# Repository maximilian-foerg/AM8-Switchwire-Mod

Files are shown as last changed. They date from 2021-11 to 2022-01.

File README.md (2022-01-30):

# AM8 Switchwire Mod

## Table of Contents
1. [Introduction](#introduction)
2. [Renders](#renders)
3. [Some Facts](#some-facts)
4. [Why Core XZ?](#why-core-xz)
5. [Printing Tips](#printing-tips)
6. [Firmware Tips](#firmware-tips)
7. [FAQ](#faq)
8. [BOM (Bill of Materials)](#bom)

## Introduction
This is a Core XZ upgrade for the popular [AM8 frame](https://www.thingiverse.com/thing:2263216) inspired by the Voron Switchwire, which also makes the AM8 compatible with VORON Afterburner.

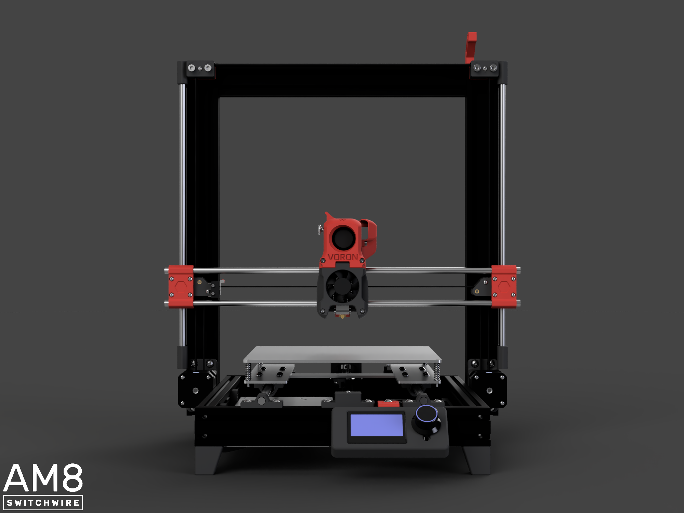
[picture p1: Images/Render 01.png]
Render 01

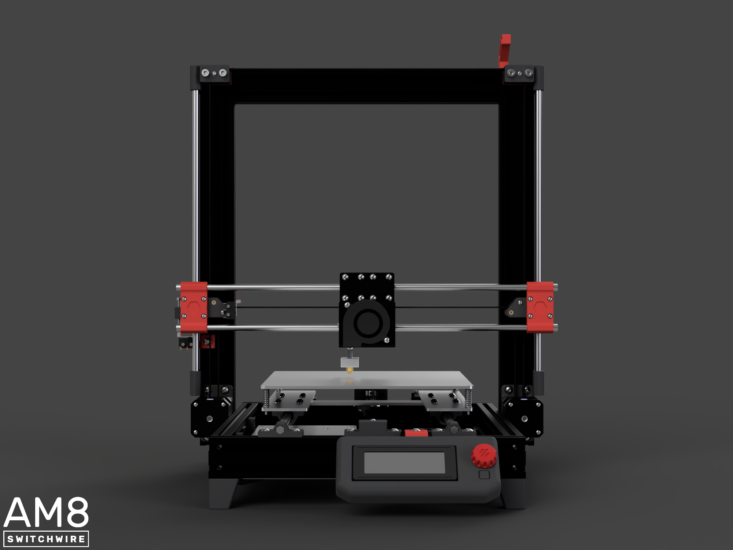
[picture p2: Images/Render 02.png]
Render 02


In case you don't know about the Voron Project, check it out at https://www.vorondesign.com/. They design outstanding open-source 3D printers, and if you're looking for a *real* upgrade, I'd suggest you build a Voron instead. It probably won't get any better.
But if you enjoy tinkering on your cheap 3D printer just like me, this mod could be something for you.

## Renders
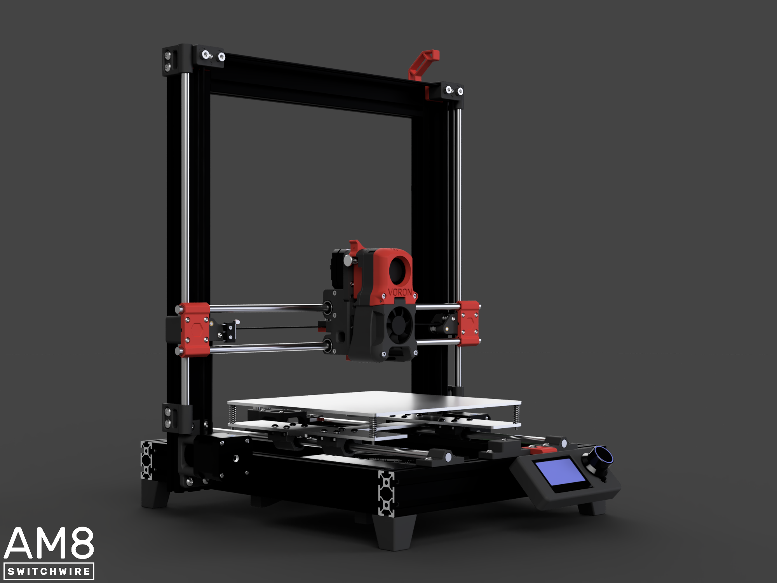
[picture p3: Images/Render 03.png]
Render 03

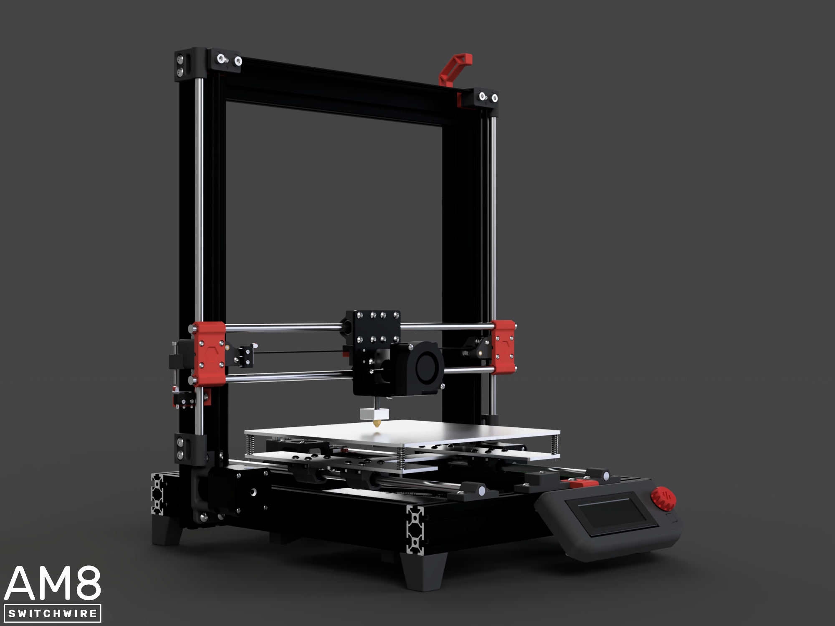
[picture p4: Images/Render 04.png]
Render 04

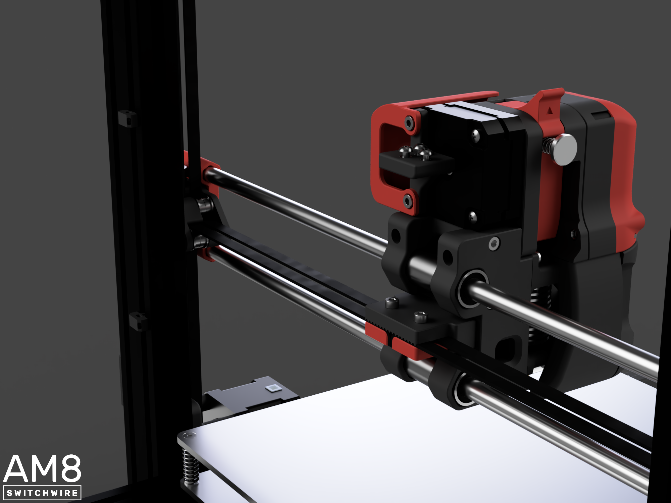
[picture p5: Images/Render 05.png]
Render 05

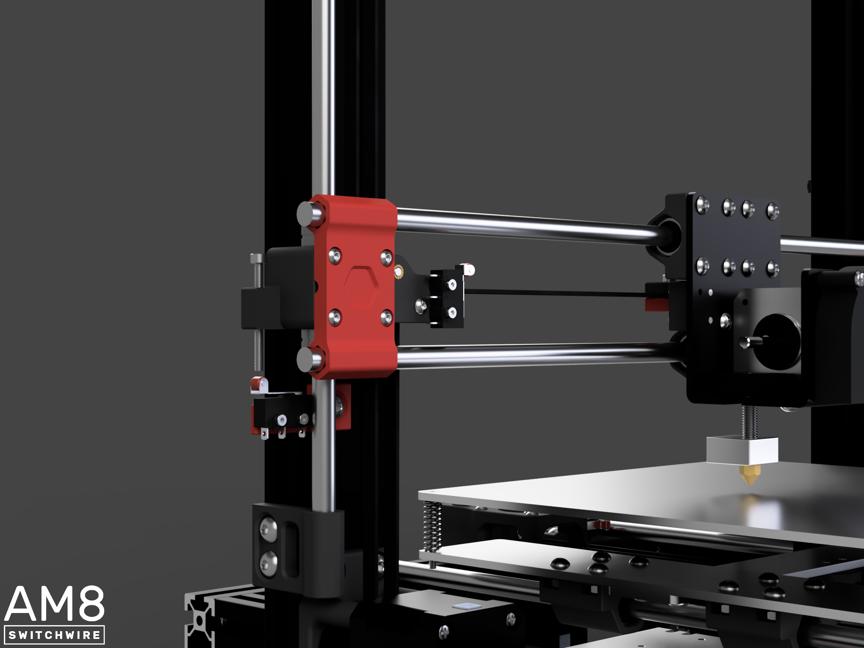
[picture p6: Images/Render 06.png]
Render 06

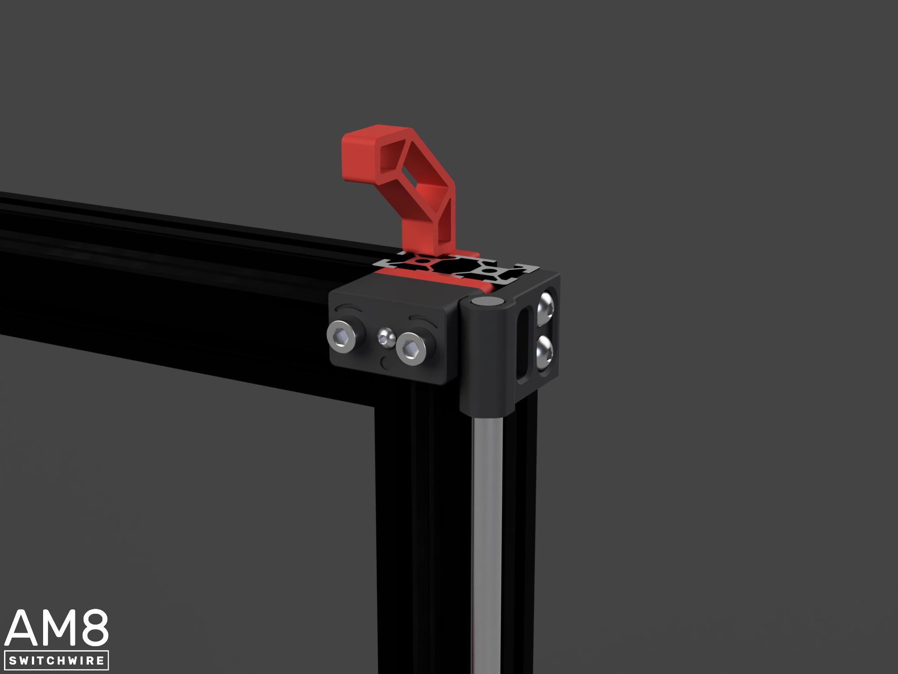
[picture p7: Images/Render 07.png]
Render 07


## Some Facts
* Build volume is 220x220x220mm with Anet A8 print head and up to 220x220x270mm with VORON Afterburner.
* The dimensions of the aluminum extrusions are the same as for the AM8.
* This upgrade uses as many of the original Anet A8 and AM8 parts as possible. Still, you will have to buy some stuff. Have a look at the [BOM](#bom).
* Although I redesigned every part, the Y axis did not change compared to the AM8. So if you already have an AM8, you can continue to use your Y axis.

**_CAUTION!_**
* Altough it would work, **you better not use the original Anet A8 board for this mod**. The Anet A8 board is designed to have two motors connected to the stepper motor driver for the Z axis. Many older versions of the board do not allow you to regulate the voltage for these motors. Since this mod only requires one stepper motor for the Z axis, it would get twice as much current as it should. This could destroy the motor. But it is a good idea to change to a more modern board anyway - especially TMC stepper motor drivers will raise the printer to a new level. My recommendation is the Bigtreetech SKR mini E3 V2. At first glance it may seem expensive, but it has TMC 2209 drivers integrated and is therefore relatively cheap. The TMC drivers allow the voltage for each stepper motor to be controlled individually by software.
* You will have to flash a new firmware (and for the time being, configure it yourself). One possibility is to use [Marlin](https://marlinfw.org/), which can be configured for Core XZ motion systems. My recommendation is [Klipper](https://www.klipper3d.org/) together with a Raspberry Pi running [Mainsail](https://docs.mainsail.xyz/). Klipper runs all calculations on the much more computationally powerful Raspberry Pi, so you can use it to compensate for the weak hardware of the original Anet A8 or other 3D printer controller boards.

## Why Core XZ?
3D printers make fast movements, so it is a great advantage if moving parts have the lowest possible mass. This is why the Core XY architecture was developed, where two stepper motors can move the print head in two directions through a sophisticated belt drive without having to move themselves. Well-known DIY Core XY printers are, for example, the [Voron 0](https://www.vorondesign.com/voron0.1), [Voron Trident](https://www.vorondesign.com/voron_trident) and [Voron 2](https://www.vorondesign.com/voron2.4), or the very popular [Hypercube](https://www.thingiverse.com/thing:1752766) and [Hypercube Evolution](https://www.thingiverse.com/thing:2254103).
However, a Core XY motion system requires a cube-shaped frame, which we do not have with the AM8. Converting the frame would contradict the sense of an "upgrade" and would rather be a completely new printer. Therefore, the [Voron Switchwire](https://www.vorondesign.com/voron_switchwire) gave me the idea to implement the Core XY architecture rotated by 90 degrees as Core XZ architecture on the AM8. This has the following advantages:
* The weight of the X axis is now balanced, because there is no longer a motor on one side.
* The X axis becomes lighter since all stepper motors are fixed to the frame.
* You get rid of the threaded spindles.
* You can make movements in the Z direction just as fast as in the X and Y directions.
* You need one less stepper motor.

## To check before modding your printer
### Extrusions
This mod is using the same aluminium extrusions as the AM8 mod. Extrusions used for designing the parts are Misumi HFSB5-2040, but any 2020 B-type nut 6 extrusions will work.
Make sure your extrusions have these lenghts:
* 3 * 310mm
* 2 * 340mm
* 2 * 440mm

A few mm more or less will work too, as long as the deviations are consistent (f.e. 3 * 313mm is fine, but 2 * 310mm and 1 * 313mm is not).

### Linear Rods
This mod assumes that the original linear rods of the Anet A8 are used. Their lengths are:
* 2 * 436mm
* 4 * 380mm

The required length of the X axis rods is the length of your shortest extrusion + 115mm. So for the spec 310mm extrusions, rods of 425mm in length are required. Longer rods will stick out on the sides, but that's ok.

## Printing Tips
* A number at the end of each file name indicates how often the part must be printed (no number = print it once).
* The `[A]` tag at the beginning of a file name means that this is an accent part. You can print it in an accent color if you like.
* All parts are already oriented for the best printing position. Do not change the orientation. They are specially designed and oriented to be printed without any supports.
* The parts HAVE to be printed in ABS, PETG or another material that can withstand mechanical stress. PLA is NOT an option. Avoid PETG if you have an enclosure for your printer or want to build one, because it bends at high ambient temperatures ("heat creep"). ABS is the best way to go here.
* The parts are designed to be printed with a 0.4mm nozzle at 0.2mm layer height. I recommend the following slicer settings:
  * 4 walls, 5 bottom layers, 5 top layers
  * 40% cubic or gyroid infill
  * No supports
  * No raft
  * Brim or skirt as needed
* Before printing, calibrate your extruder steps and the temperature and flow rate for your specific filament. Get rid of any strining, warping and elephant food on your prints. There are tons of tutorials on the web on how to do each of that.

## Firmware Tips
This sections contains some tips for firmware configuration. Note that the firmware directory contains some configurations.

### General
* Min. Y position: 0
* Max. Y position: 220
* Min. Z position: 0
* Z hop before homing: 5
* DO NOT disable stepper motors (g-code command `M84`) after prints. Print head would fall down on print or bed.
### Anet A8 print head
* Min. X position: -24
* Max. X position: 225
* Max. Z position: 220
* Choose a z hop > 30 if using a level probe instead of the Z endstop switch. This is necessary because if the printhead falls next to the bed after power off, the nozzle protrudes about 30mm below the bed.
### VORON Afterburner print head
* Min. X position: -13
* Max. X position: 240
* Max. Z position: 250

## FAQ
### Why are there three versions of the XZ Axis X Rod Mount (40, 45 and 46mm)?
There are two versions of the Anet A8, one with 45mm spacing between the linear rods of the X-axis, and one with 46mm spacing. This also means that the ball bearings on the print head are either 45mm or 46mm apart. You need to find out which version of the Anet A8 you have, and print the appropriate version of the rod mounts. The 40mm rod mounts are needed for the VORON Afterburner.

## BOM
The following lists specify which additional parts you'll need to upgrade your existing printer to this mod. Note that there are alternative standards for each DIN standard (for example, the corresponding ISO standard). These are just the standards I used to design the parts. If you decide to use other nuts and bolts, check the dimensions beforehand. This is especially important for nuts and countersunk screws, less so for button head screws and cylindrical head screws.

### If you want to keep your Y axis:
| Item | Amount | Comment |
| ---- | :----: | --- |
| DIN 934 M2 nut | 4 | Only 2 if you're not using the Z endstop |
| DIN 912 M2x10 screw | 4 | Only 2 if you're not using the Z endstop |
| ISO 7380 M3x25 screw | 4 |
| ISO 7380 M3x30 screw | 18 |
| DIN 912 M3x30 screw or any other M3 screw with 30-40mm in length | 1 | Only if you ARE using the Z endstop |
| ISO 7380 M5x10 screw | 17 | Only 16 if you're not using the Z endstop |
| DIN 912 M5x30 screw | 4 |
| M5 T-Nut for 2020 | 21 | Only 20 if you're not using the Z endstop |
| DIN 988 6x3x0.5 precision shim ring | 16 | YES, measurements are important, and NO, you can't just use cheap M3 washers |
| GT2 16T timing pulley | 1 | 3 needed in total, but 2 are already included with Anet A8 |
| GT2 timing belt with 6mm width | ~5m | Glassfiber belt recommended, and it's highly recommended to replace the Y axis belt too |
| F623 ball bearing | 16 |
| Threaded heat insert M3x5x4 | 15 | The ones VORON printers use; Only 14 if you're not using the Z endstop |

### If you want to upgrade your Y axis, you'll ALSO need:
| Item | Amount | Comment |
| ---- | :----: | --- |
| DIN 912 M2x14 screw | 2 |
| DIN 934 M2 nut | 2 |
| DIN 934 M3 nut | 1 |
| ISO 7380 M3x16 screw | 1 | DIN 912 or other button head would work too, length should be 16-18mm |
| ISO 7380 M3x30 screw | 4 |
| ISO 7380 M5x10 screw | 10 | You may already have these from your AM8 |
| DIN 912 M5x30 screw | 2 |
| M5 T-Nut for 2020 | 12 | You may already have these from your AM8 |
| DIN 988 6x3x0.5 precision shim ring | 2 | Again, measurements are important |
| F623 ball bearing | 2 | Came with A8 |

### Print Heads
#### Original Anet A8
| Item | Amount |
| ---- | :----: |
| DIN 934 M3 nut | 2 |
| DIN 912 M3x12 screw | 2 |

#### VORON Afterburner
For the adapter and belt clamp, you need (some may also be listed in the official sourcing guide):
| Item | Amount | Comment |
| ---- | :----: | --- |
| DIN 934 M3 nut | 2 |
| DIN 912 M3x12 screw | 4 |
| DIN 912 M3x20 screw | 2 | Only if you are using the PL-08N probe |
| DIN 912 M3x30 screw | 2 |
| DIN 912 M3x40 screw | 3 |
| Threaded heat insert M3x5x4 | 9 | Only 7 if you're NOT using the PL-08N probe |
| LM8LUU linear bearing | 2 | Misumi recommended. Short LM8UU bearings of Anet A8 print head NOT compatible. |

For the rest of the items, please refer to the official VORON sourcing guide: https://www.vorondesign.com/sourcing_guide (select 'VORON Afterburner' at the bottom).

For the printed parts, you can download Switchwire's repository: https://github.com/VoronDesign/Voron-Switchwire (click on _Code_ -> _Download ZIP_). You will find the STLs under `STL/Gantry/XZ_Axis/X_Carriage`.
Print the following:
* `[a]_blower_housing_front.stl`
* `blower_housing_rear.stl`
* `hotend_fan_mount.stl`
* `Direct_Feed/[a]_connector_cover.stl` (If you like, but it isn't really compatible)
* `Direct_Feed/[a]_guidler.stl`
* `Direct_Feed/[a]_latch.stl`
* `Direct_Feed/[a]_latch_shuttle.stl`
* `Direct Feed/extruder_body.stl`
* `Direct_Feed/extruder_motor_plate.stl`
* And every part under `Printheads/X` for print head X of your choice

### Accessories
Required parts for optional accessories.

#### Print Head Cable Duct
| Item | Amount |
| ---- | :----: |
| ISO 7380 M5x10 screw | 1 |
| M5 T-Nut for 2020 | 1 |
| Zip tie | 3 |

#### Feet
| Item | Amount |
| ---- | :----: |
| ISO 7380 M5x10 screw | 4 |
| M5 T-Nut for 2020 | 4 |

#### LCD Controller Mount
| Item | Amount |
| ---- | :----: |
| ISO 7380 M3x10 screw | 2 |
| ISO 7380 or DIN 912 M3x12 screw | 4 |
| ISO 7380 M5x10 screw | 1 |
| M5 T-Nut for 2020 | 1 |
| Threaded heat insert M3x5x4 | 2 |

From the VORON Switchwire repository (link above), print everything...
* ... from directory `STL/Electronics/LCD/2004 (Prusa)` for LCD 2004 controller
* ... or from directory `STL/Electronics/LCD/Mini12864` for Mini 12864 LCD controller

#### Lightweight LM8UU Bearing Blocks
| Item | Amount | Comment |
| ---- | :----: | --- |
| DIN 934 M4 nut | 4 | Per block |
| ISO 7380 M4x8 screw | 4 | Per block; Different screw heads are fine too (no countersunk) |

#### Other
* Print some **2020 Cable Clips** for cable management with zip ties.
* From the Switchwire repository ypu can print:
  * `STL/Electronics/skr_mini_e3_mount.stl` to mount the recommended SKR Mini E3 board
  * `STL/Electronics/raspberry_pi_mount.stl` to mount a Raspberry Pi
  * or `STL/Electronics/raspberry_pi_zero_shelf` to mount a Raspberry Pi Zero on the SKR Mini E3, which results in a cheap and compact control unit. There's a great [video](https://www.youtube.com/watch?v=AtW3GqkKUz8) about how to connect them.

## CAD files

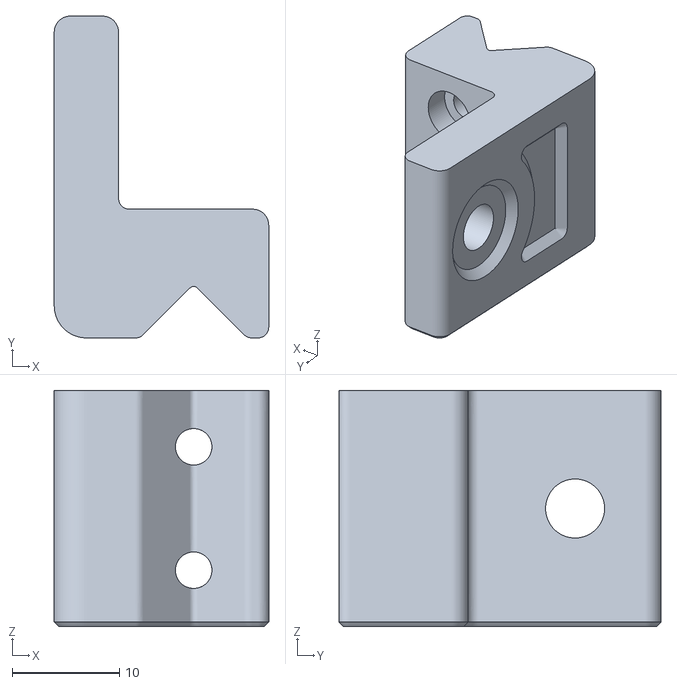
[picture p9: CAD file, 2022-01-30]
STLs/Accessories/[A] LCD Controller Mount.stl
20.0 x 30.0 x 22.0

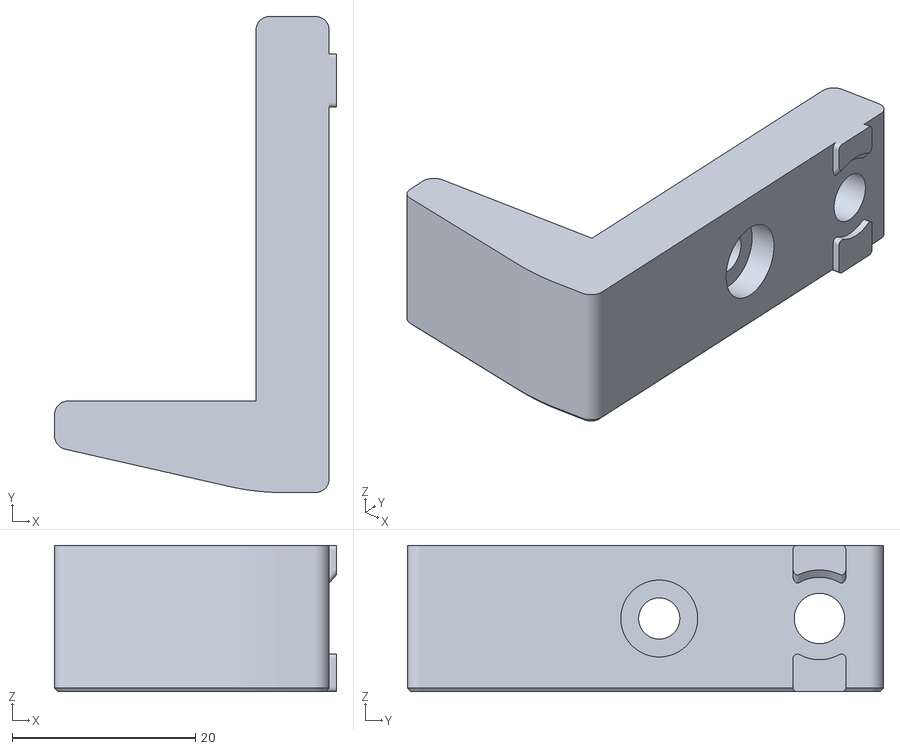
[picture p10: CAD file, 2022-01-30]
STLs/Electronics/MeanWell LRS-350-24 Mount 2x.stl
30.8 x 52.0 x 16.0

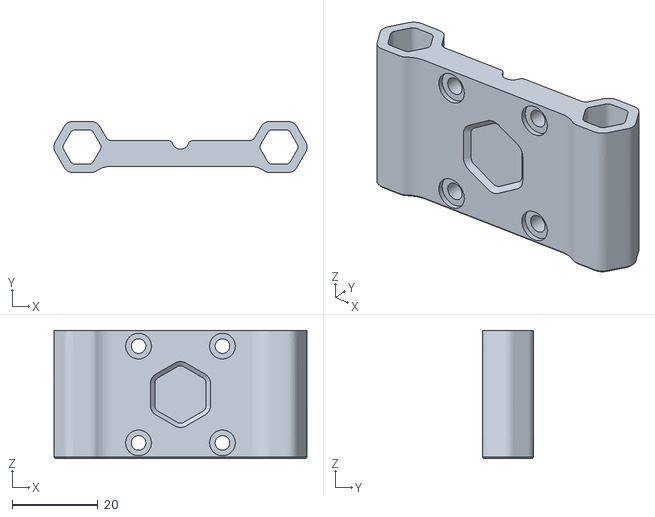
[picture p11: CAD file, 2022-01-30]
STLs/XZ Axis/Printheads/Anet A8/[A] X Rod Mount (46mm) 2x.stl
59.1 x 12.0 x 30.0

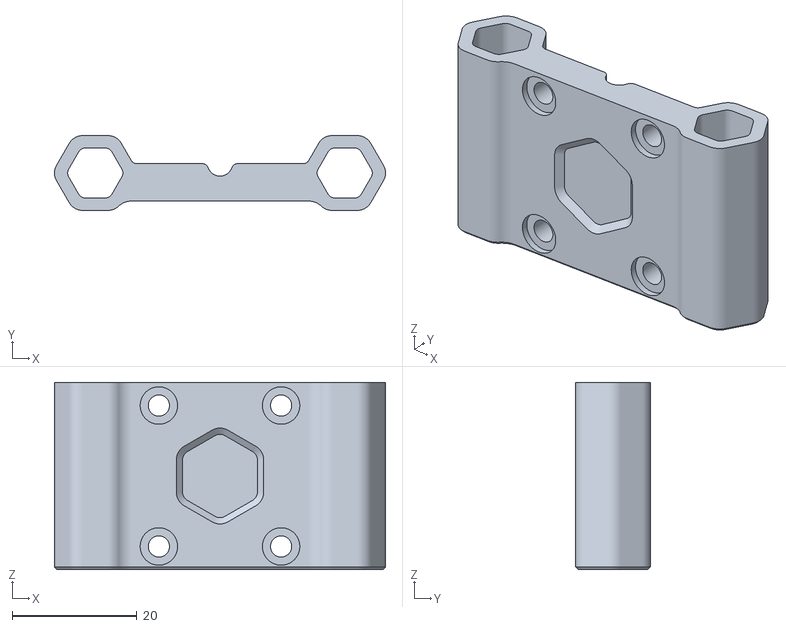
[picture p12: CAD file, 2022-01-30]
STLs/XZ Axis/Printheads/VORON Afterburner/[A] X Rod Mount (40mm) 2x.stl
53.1 x 12.0 x 30.0

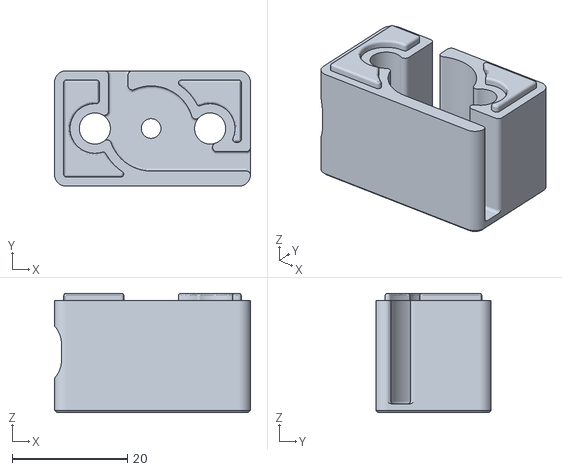
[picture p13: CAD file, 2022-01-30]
STLs/XZ Axis/XZ Idler Pulley Mount Left A.stl
34.0 x 20.0 x 20.7

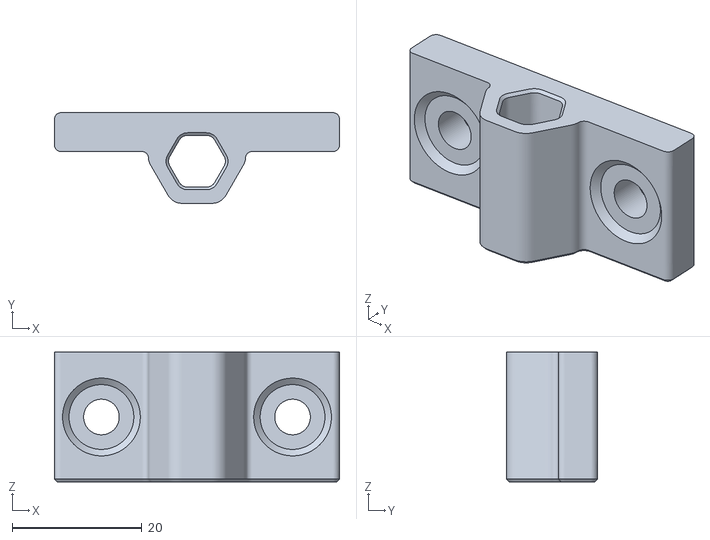
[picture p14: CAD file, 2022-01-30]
STLs/Y Axis/Y Rod Mount 3x.stl
44.0 x 14.0 x 20.0

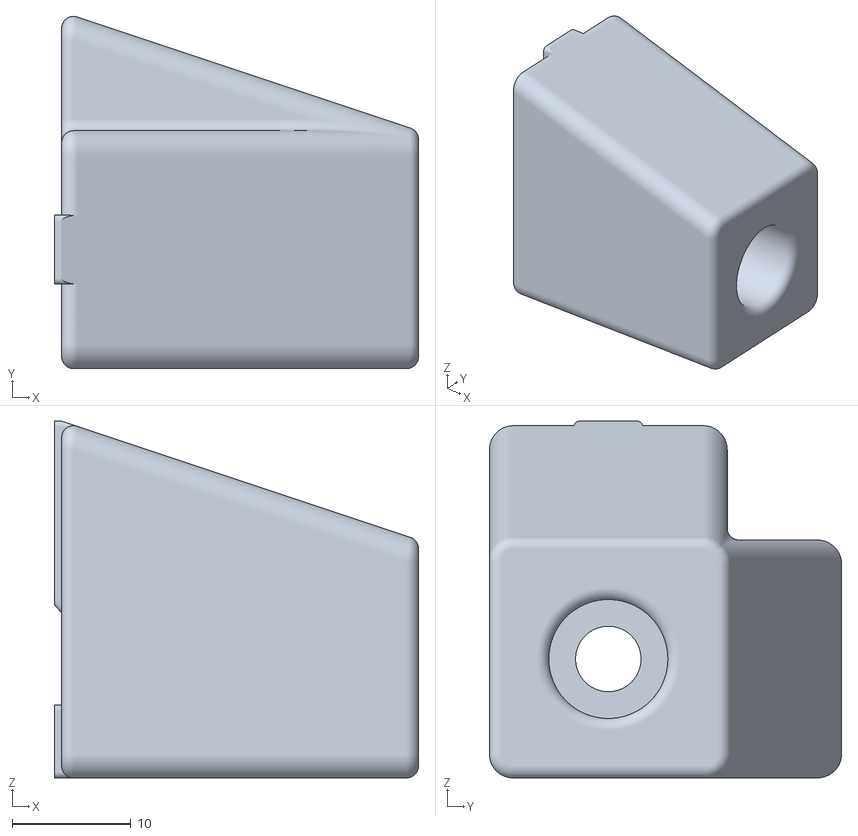
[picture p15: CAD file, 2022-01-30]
STLs/Accessories/Foot Left 2x.stl
30.6 x 29.6 x 30.0

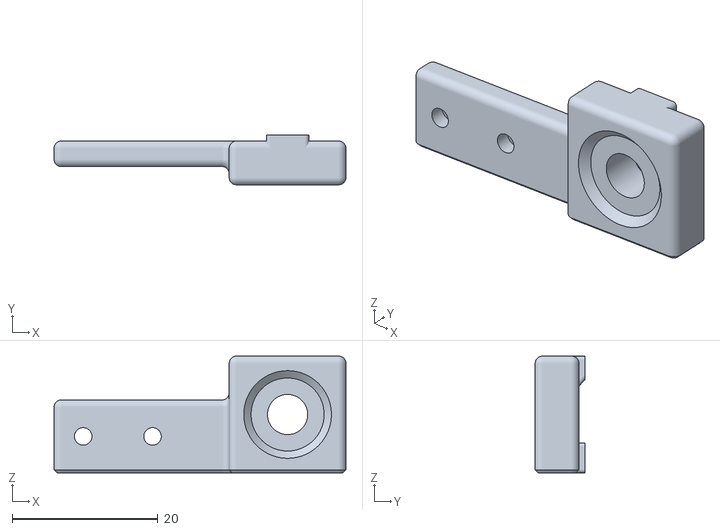
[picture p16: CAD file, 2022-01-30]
STLs/XZ Axis/[A] Z Endstop Mount.stl
40.0 x 6.80 x 16.0

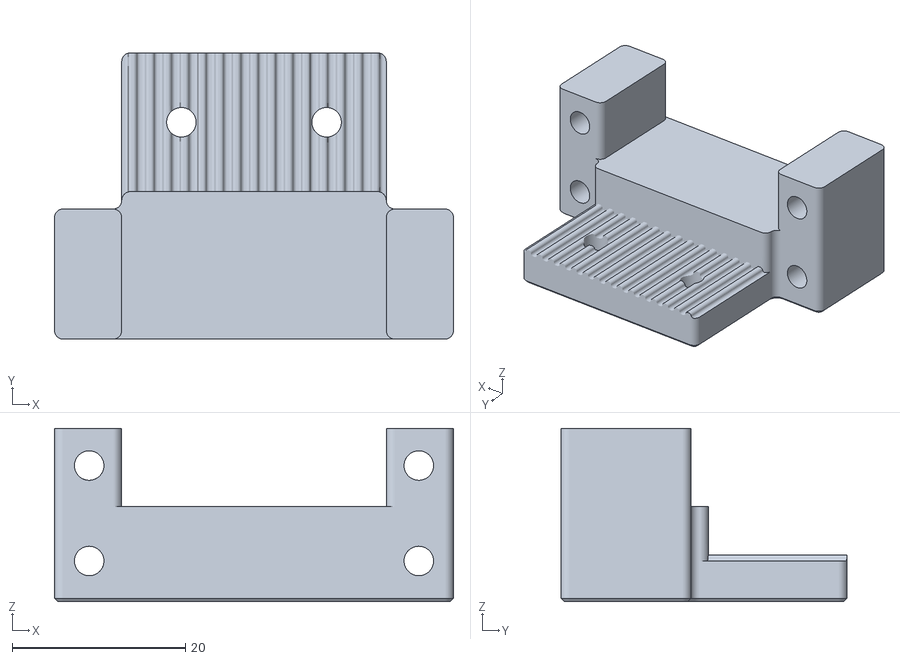
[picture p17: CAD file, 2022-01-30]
STLs/XZ Axis/Printheads/Anet A8/Belt Clamp Body.stl
46.0 x 33.0 x 20.0

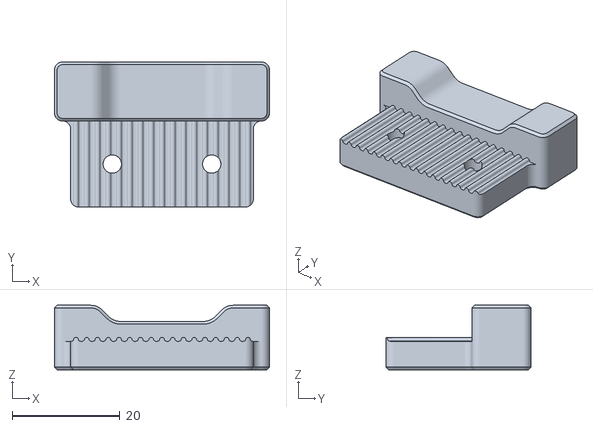
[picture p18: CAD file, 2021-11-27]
STLs/XZ Axis/Printheads/VORON Afterburner/Belt Clamp Body.stl
40.0 x 27.0 x 12.0

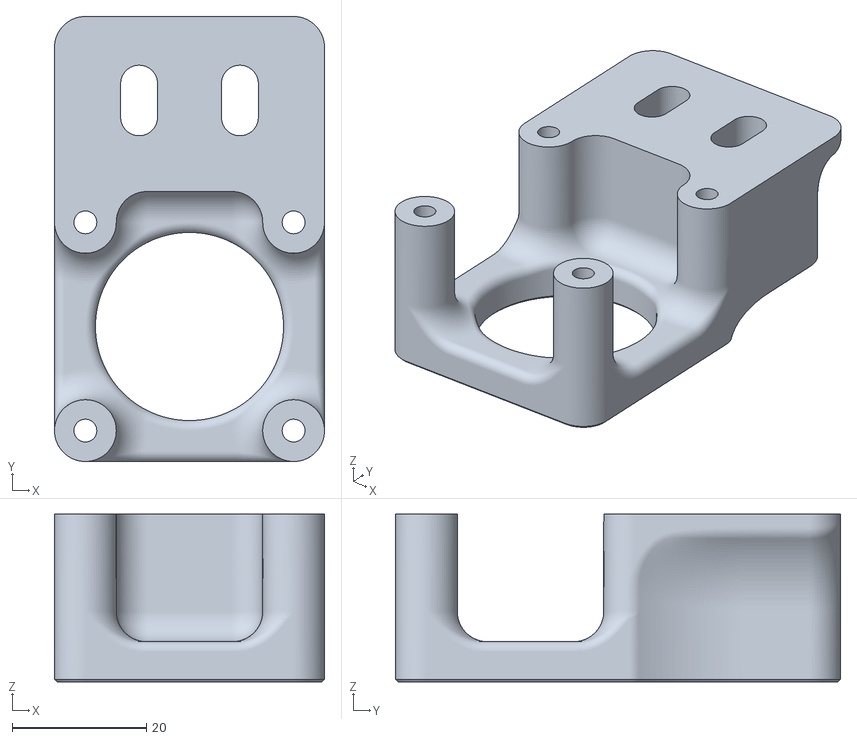
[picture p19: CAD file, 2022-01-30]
STLs/Y Axis/Y Motor Mount.stl
40.2 x 66.3 x 25.0

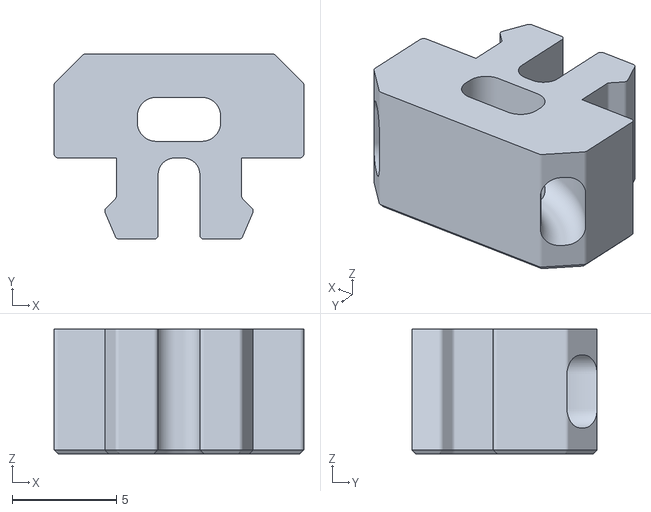
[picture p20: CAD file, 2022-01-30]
STLs/Accessories/2020 Cable Clip.stl
12.0 x 8.90 x 6.00

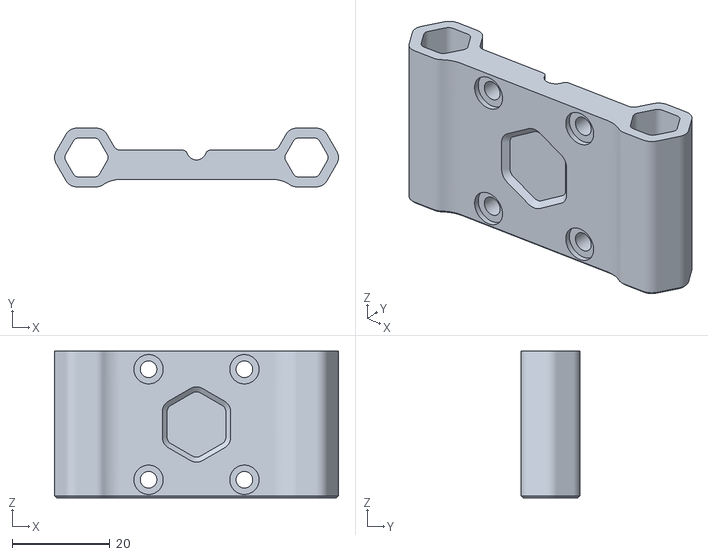
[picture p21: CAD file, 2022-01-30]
STLs/XZ Axis/Printheads/Anet A8/[A] X Rod Mount (45mm) 2x.stl
58.1 x 12.0 x 30.0

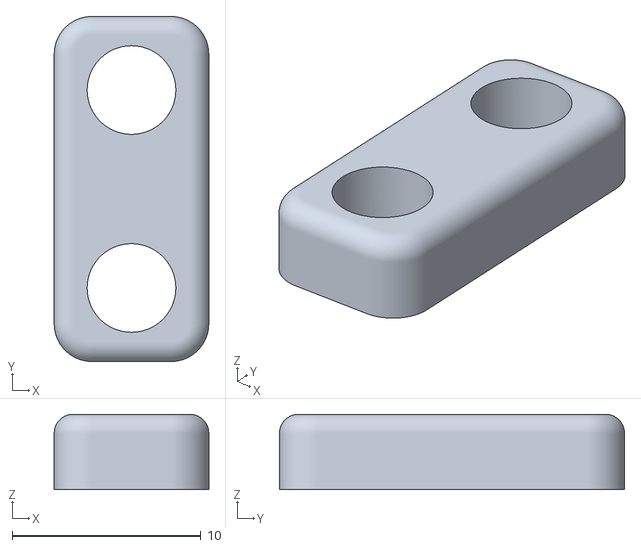
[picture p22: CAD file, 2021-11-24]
STLs/XZ Axis/Printheads/VORON Afterburner/PL-08N Probe Bracket 1x.stl
8.20 x 18.3 x 4.00

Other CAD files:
STLs/XZ Axis/Z Rod Mount 4x.stl
STLs/Y Axis/Y Rod Mount with Endstop.stl
STLs/Accessories/Lightweight LM8UU Bearing Block 7x.stl
STLs/XZ Axis/Printheads/Anet A8/Belt Clamp Lid 2x.stl
STLs/Accessories/Foot Right 2x.stl
STLs/Accessories/Printhead Cable Duct.stl
STLs/XZ Axis/Printheads/VORON Afterburner/Belt Clamp Lid 2x.stl
STLs/XZ Axis/Printheads/VORON Afterburner/VORON Afterburner Adapter Left.stl
STLs/XZ Axis/Printheads/VORON Afterburner/VORON Afterburner Adapter Right.stl
STLs/XZ Axis/XZ Idler Pulley Mount Right A.stl
STLs/XZ Axis/XZ Joint Left A.stl
STLs/XZ Axis/XZ Joint Left B with Z Endstop Screw.stl
STLs/XZ Axis/XZ Joint Left B.stl
STLs/XZ Axis/XZ Joint Right A.stl
STLs/XZ Axis/XZ Joint Right B.stl
STLs/XZ Axis/X_Z Motor Mount 2x.stl
STLs/XZ Axis/[A] XZ Idler Pulley Mount Left B.stl
STLs/XZ Axis/[A] XZ Idler Pulley Mount Right B.stl
STLs/Y Axis/Belt Clamp.stl
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

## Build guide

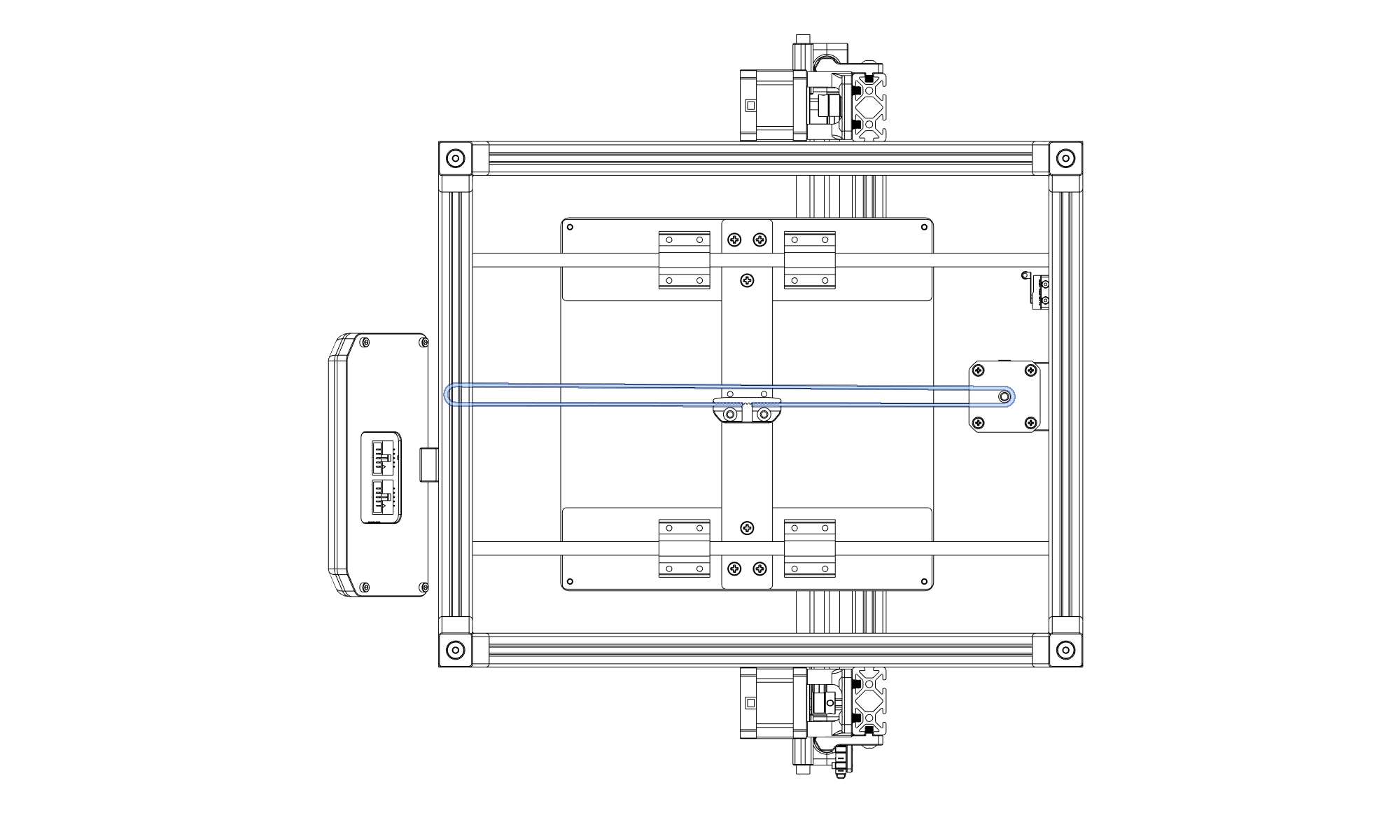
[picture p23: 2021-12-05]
Manual/Y belt path.png

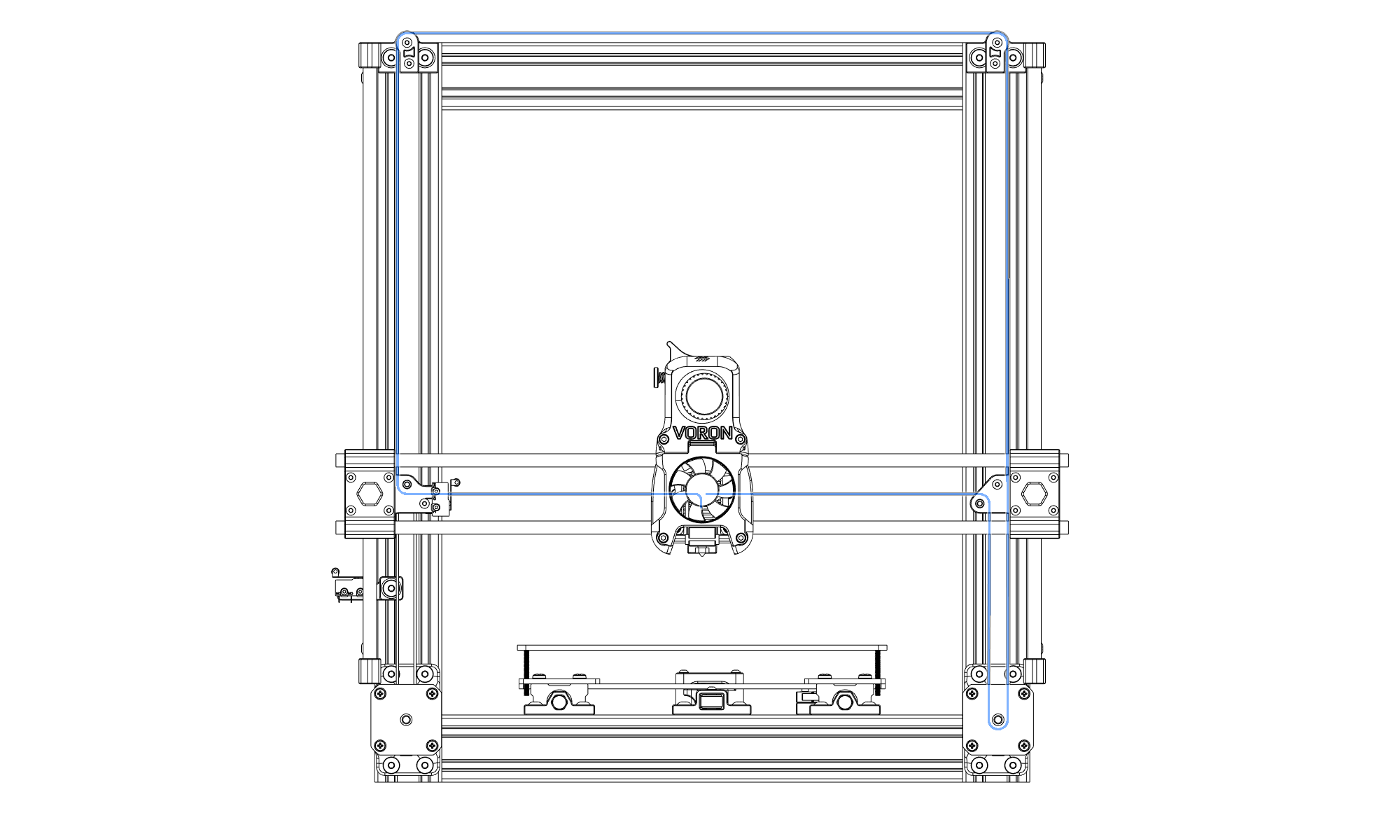
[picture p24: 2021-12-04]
Manual/Z Belt Path.png

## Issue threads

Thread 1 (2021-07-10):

Enclosure ?

extremeshok, 2021-07-10:
Since the guide rails are located on the outside, it would appear your design is not able to have a neat enclosure like a true switchwire.

maximilian-foerg, 2021-07-10:
That is absolutely correct because that is not a true Switchwire. If you want a Switchwire, build a Switchwire. I would not recommend building an enclosure for this printer. The effort and cost of doing so is not worth it in the face of much more important upgrades. The printer much more urgently needs a better extruder, a better hotend, a lighter printhead, automatic bed leveling, and a better print bed. An enclosure is the last thing I would improve on this printer. With all these improvements, though, you're probably getting pretty close in price to a Voron Swicthwire, so you could have built a Swicthwire right away. I'm also not positioning this printer as an alternative to the Voron Switchwire.

waym99, 2022-01-19:
While that is definitly true. I think it might be worth the effort to create a customized enclosure, since there are a lot of people out there already having upgraded much of the things you have mentioned. It is definitly not an alternative to the Switchwire but more a fun project for modders. There are already quite a few good ender 3 switchwire mods. I think this could also be a good one.

maximilian-foerg, 2022-01-19:
Maybe there will be a V2 which brings the printer closer to a Switchwire. By arranging the aluminum extrusions in a different way, a Switchwire-like shape can be achieved, which makes a compact enclosure possible.

waym99, 2022-01-19:
yeah definitly. If you need some help I am up for that. Coming also from germany should make the communication quite easy.

Closed 2021-07-10.

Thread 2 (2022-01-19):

Full CAD

waym99, 2022-01-19:
Do you mind sharing with us the complete model and all its versions as step or even better f3d file?

maximilian-foerg, 2022-01-19:
I included the step file in every commit, so you can already access every version of the step file via the repositories history. Full f3d file will come soon

waym99, 2022-01-19:
Full f3d would be awsome! Working on an enclosure and I think the afterburner mod is messing.

maximilian-foerg, 2022-01-30:
Files are up

Closed 2022-01-30.

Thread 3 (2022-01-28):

Brass Inserts

MistrPC, 2022-01-28:
I see from your supplied pictures, there are some parts that require brass inserts, do you have a list of which parts need the inserts?   Great Build by the way!!

Adonay944, 2022-02-09:
I suggest you open the STEP File in your favorite cad software or viewer that way you can study the whole construction in detail.

Closed 2022-02-12.

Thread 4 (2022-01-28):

Afterburner Carriage Missing from Step File

leadgtr7, 2022-01-28:
HI,
I couldn't find the CAD for the afterburner carriage only for the stock A8

Can this be added?

maximilian-foerg, 2022-01-29:
The original f3d file will be added soon. It will contain all parts.

maximilian-foerg, 2022-01-30:
Files are up

Closed 2022-01-30.

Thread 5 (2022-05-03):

Is it possible to move the gantry endstop to the toolhead?

W141-ID, 2022-05-03:
I think it would make the wiring much cleaner! If you have any time doing this it would be awesome. I have seen it on different afterburner mods (https://github.com/kevinakasam/AfterburnerEnder3)

Closed 2023-05-25.

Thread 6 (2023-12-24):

working on a voron tap compatible x carriage

Golgomaph, 2023-12-24:
Hi Max,

thank your for your awesome looking modification.
Currently im planning to do this conversion on my Anet A8 and because i enjoy Voron Tap Probing in my 2.4 im heavily interested in using it on your AM8-Switchwire.

I therefore spent some hours in Fusion and tried to modify your X Carriage, making it compatible with the Tap-Baseplate. Photo attached.

Would love to here your feedback and ideas in improving the design based on your experience on this printer mod. Hopefully i did not oversee a STL-File hiding in a subfolder and provided specifically for my need... this happened to me in the past sometimes.

Cheers!
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

maximilian-foerg, 2023-12-25:
Hi! Thank you, always happy to see people having interest in this mod!

Sadly, I have no experience with Voron Tap. But your design looks good to me so far, it's probably the approach I would have gone for too. It's just that I have concerns about nozzle probing on bedswingers in general, as the usually aren't sturdy enough. Especially for Switchwire it is not recommended to use Tap, since its bed is only fixed in the center. So maybe it can work for the Anet A8 bed, as it is fixed in all 4 corners. I'd definitely replace the bed springs with fixed metal spacers and keep the probing speeds quite low!

Would love to see updates on this! If you like, you can create a PR to share this mod with others when it's done. Just create a folder structure like `Mods/Golgomaph/Voron-Tap/` and put the CAD, STLs and a README in there :)

Golgomaph, 2023-12-25:
Very wise words.

Tap recommends a rigidity of the used printbed which withstands the probing force of the tap and excludes the switchwire bed in the same sentence. I will dig deeper on that, since im planning to switch to another bed setup anyway.

Will keep you updated. Im very new to github and might need some help in integrating this mod to your repo later, however thats far future talking.

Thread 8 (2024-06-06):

Suggested Mods/build experience

agreen, 2024-06-06:
Apologies for creating this as an issue. Not really a better way to share it.

I'm in the process (nearly done) on rebuilding my AM8 into one of these.

Some changes/feedback I have are:

- Using Stealthburner and a BLTouch for Z homing.  I had a hard time figuring this out, but the mount is essentially a Voron Legacy mount. You could use either the stock Voron Legacy mount (from the voron repo) or this one, which includes the BLTouch mounting option - https://www.printables.com/model/458163-voron-legacy-carriage-mount-with-integrated-bltouc  Also, FYI, the original mount is an afterburner mount, which isn't 100% compatible with stealthburner, but the stealthburner mount is backward compatible.
- Using a toolhead CAN board, because I had one "laying around".  This helps clean up the look I think, but I wanted to still use limit switches as I'm not a huge fan of sensorless homing.   This presents two issues... 1. I'd like to delete the switch mount for the XZ Joint left, and make it look the same as the XZ joint right.  2. Need to locate a place on the toolhead to mount an X Limit switch.  Seems like maybe the belt clamp could be a good candidate, but haven't fully figured it out yet.
- I printed/used these stiffening parts, similar to the original AM8, to make the printer more solid.  Issue is, I need to design some kind of foot now.  My original build used some rubber feet screwed into the corners of those, which is what I'm still doing currently. Could either leave it or go with something to raise it up a bit more. I haven't installed the screen, so when I do I might feel I need to, to support the screen.  https://www.thingiverse.com/thing:3128300
- I'm looking for a jacking screw method of tightening the belts, vs the "pull and tighten" design they are currently.  I recently built an Enderwire and it was nice to have jacking screws to tighten it more accurately.
- I'd like to have some deck panels to keep things from falling onto the electronics.  Going to look into designing something once I get the machine fully assembled.

Overall though, thanks very much for putting this together. Everything was straightforward to print and it's looking really nice.  I'll take osm epictures once I'm done.

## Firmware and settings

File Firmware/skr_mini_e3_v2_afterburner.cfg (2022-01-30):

# This file contains common pin mappings for the BIGTREETECH SKR mini
# E3 v2.0. To use this config, the firmware should be compiled for the
# STM32F103 with a "28KiB bootloader" and USB communication. Also,
# select "Enable extra low-level configuration options" and configure
# "GPIO pins to set at micro-controller startup" to "!PA14".

# The "make flash" command does not work on the SKR mini E3. Instead,
# after running "make", copy the generated "out/klipper.bin" file to a
# file named "firmware.bin" on an SD card and then restart the SKR
# mini E3 with that SD card.


## Webclient config files. Uncomment one depending on UI being used.
#[include mainsail.cfg]
#[include fluidd.cfg] 


############################################################
# X Stepper Settings
############################################################

[stepper_x]
step_pin: PB13
dir_pin: !PB12
enable_pin: !PB14
rotation_distance: 32
microsteps: 16
full_steps_per_rotation: 200
endstop_pin: ^!PC0
position_min: -13
position_endstop: -13
position_max: 240
homing_speed: 80

[tmc2209 stepper_x]
uart_pin: PC11
tx_pin: PC10
uart_address: 0
run_current: 0.580
stealthchop_threshold: 999999


############################################################
# Y Stepper Settings
############################################################

[stepper_y]
step_pin: PB10
dir_pin: PB2
enable_pin: !PB11
rotation_distance: 32
microsteps: 16
full_steps_per_rotation: 200
endstop_pin: ^!PC1
position_min: 0
position_endstop: 0
position_max: 220
homing_speed: 80

[tmc2209 stepper_y]
uart_pin: PC11
tx_pin: PC10
uart_address: 2
run_current: 0.580
stealthchop_threshold: 999999


############################################################
# Z Stepper Settings
############################################################

[stepper_z]
step_pin: PB0
dir_pin: !PC5
enable_pin: !PB1
rotation_distance: 32
microsteps: 16
full_steps_per_rotation: 200
endstop_pin: probe:z_virtual_endstop
position_max: 220

[tmc2209 stepper_z]
uart_pin: PC11
tx_pin: PC10
uart_address: 1
run_current: 0.580
stealthchop_threshold: 999999


############################################################
# Extruder Stepper Settings
############################################################

[extruder]
step_pin: PB3
dir_pin: PB4
enable_pin: !PD2
rotation_distance: 21.565
microsteps: 16
full_steps_per_rotation: 200
gear_ratio: 50:17
nozzle_diameter: 0.4
filament_diameter: 1.75
max_extrude_only_distance: 100.0
pressure_advance: 0.04 # Perform a pressure advance tuning for your filament
heater_pin: PC8
sensor_type: NTC 100K MGB18-104F39050L32
sensor_pin: PA0
min_temp: 0
max_temp: 270
# Do not use the following values - perform a PID calibration!
control: pid
pid_kp: 21.177
pid_ki: 1.120
pid_kd: 100.060

[tmc2209 extruder]
uart_pin: PC11
tx_pin: PC10
uart_address: 3
run_current: 0.650
stealthchop_threshold: 0


############################################################
# Bed Settings
############################################################

[heater_bed]
heater_pin: PC9
sensor_type: NTC 100K MGB18-104F39050L32
sensor_pin: PC3
min_temp: 0
max_temp: 120
# Do not use the following values - perform a PID calibration!
control: pid
pid_kp: 67.669
pid_ki: 0.542
pid_kd: 2113.804

[bed_mesh]
speed: 80
horizontal_move_z: 5
mesh_min: 20,20
mesh_max: 200,200
probe_count: 6,6
mesh_pps: 2,2
algorithm: bicubic
bicubic_tension: 0.2


############################################################
# Homing and Bed Leveling
############################################################

[probe]
pin: ^!PC2
x_offset: 0.0
y_offset: 25.0
z_offset: 2.0 # Adjust with probe_calibrate
speed: 15
samples: 2

[safe_z_home]
home_xy_position: 110,110
speed: 80
z_hop: 5
z_hop_speed: 20

[screws_tilt_adjust]
screw1: 25,0
screw1_name: front left screw
screw2: 195,0
screw2_name: front right screw
screw3: 195,170
screw3_name: rear right screw
screw4: 25,170
screw4_name: rear left screw
horizontal_move_z: 5
speed: 80
screw_thread: CW-M3


############################################################
# Mechanics and Electronics
############################################################

[printer]
kinematics: corexz
max_velocity: 200
max_accel: 2000
max_accel_to_decel: 2000
square_corner_velocity: 5.0
max_z_velocity: 100
max_z_accel: 1000

[mcu]
serial: # See https://www.klipper3d.org/Installation.html
restart_method: command

[fan]
pin: PC6
off_below: 0.1

[heater_fan hotend_fan]
pin: PC7
off_below: 0.1
heater: extruder

[idle_timeout]
timeout: 600 # 10 minutes
gcode:
    TURN_OFF_HEATERS
    M107 ; Turn off fans
    SET_STEPPER_ENABLE STEPPER=stepper_y ENABLE=0
    SET_STEPPER_ENABLE STEPPER=extruder ENABLE=0


############################################################
# Macro Definitions
############################################################

[gcode_macro START_PRINT]
gcode:
    G28                            ; Home
    G92 E0                         ; Zero the extruder

[gcode_macro END_PRINT]
gcode:
    G92 E0                         ; Zero the extruder
    G1 E-5 F3600                   ; Retract filament
    TURN_OFF_HEATERS
    M107                           ; Turn off fans
    G91                            ; Relative positioning
    G0 Z3 F3600                    ; Move nozzle up
    G90                            ; Absolute positioning
    G28 X                          ; Home X
    G0 Y220                        ; Move bed to front

    # Disable extruder and Y stepper
    SET_STEPPER_ENABLE STEPPER=stepper_y ENABLE=0
    SET_STEPPER_ENABLE STEPPER=extruder ENABLE=0

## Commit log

2021-05-24 Added CAD step file
2021-06-03 Finished Y and XZ Axis
    [XZ Axis Left Nema 17 Mount 1x.stl, XZ Axis Left Pulley Mount 1x.stl, XZ Axis Left XZ Joint Base 1x.stl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]
2021-06-03 Added original Anet A8 toolhead option
    [Belt Adapter for Anet A8 Toolhead (Base).stl, Belt Adapter for Anet A8 Toolhead (Lid).stl]
2021-06-03 Optimized Anet A8 Belt Adapter for faster printing
    [Belt Adapter Base (for Anet A8 Toolhead) 1x.stl, Belt Adapter Lid (for Anet A8 Toolhead) 1x.stl, Belt Adapter for Anet A8 Toolhead (Base).stl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]
2021-06-04 Made belt adapter for Anet A8 toolhead narrower to allow full X movement
    [Belt Adapter Base (for Anet A8 Toolhead) 1x.stl]
2021-06-05 Added endstop mounts for X and Z axis
    [XZ Axis Left XZ Joint Base 1x.stl, XZ Axis XZ Joint Rod Clamp 2x.stl, Z Axis Endstop Bracket 1x.stl]
2021-06-05 Corrected rod clamp printing orientation
    [XZ Axis XZ Joint Rod Clamp 2x.stl]
2021-06-06 Changed default X axis rod distance to 46mm
    [Belt Adapter Base (for Anet A8 Toolhead) 1x.stl, XZ Axis Right XZ Joint Base 1x.stl, XZ Axis XZ Joint Rod Clamp (45mm) 2x.stl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]
2021-06-16 Removed unnecessary screws from XZ joints
    [XZ Axis Left XZ Joint Base 1x.stl, XZ Axis Right XZ Joint Base 1x.stl, XZ Axis XZ Joint Rod Clamp (45mm) 2x.stl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]
2021-06-16 Updated CAD
2021-06-16 Added BOM for AM8 users
2021-06-16 Minor BOM edits
2021-06-16 Corrected screw hole positions on XZ axis motor mounts
    [XZ Axis Left Nema 17 Mount 1x.stl, XZ Axis Right Nema 17 Mount 1x.stl, XZ Axis XZ Joint Rod Clamp (45mm) 2x.stl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]
2021-06-18 Made XZ joints easier to assemble; Reinforced XZ axis pulley mounts
    [XZ Axis Left Pulley Mount 1x.stl, XZ Axis Left XZ Joint Base 1x.stl, XZ Axis Left XZ Joint Lid 1x.stl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]
2021-06-18 Updated 45mm rod clamp STL
    [XZ Axis XZ Joint Rod Clamp (45mm) 2x.stl]
2021-06-19 Minor reinforcment of Z axis rod clamps
    [Z Axis Linear Rod Mount 2x.stl, Z Axis Linear Rod Mount Mirrored 2x.stl]
2021-06-20 Minor design improvements; Moved gantry back by 10mm to allow full Y motion range
    [XZ Axis Left Pulley Mount 1x.stl, XZ Axis Right Pulley Mount 1x.stl, Y Axis Nema 17 Mount 1x.stl]
2021-06-26 Belt Adapter for Anet A8 Toolhead now has two clamps; Added printing tips to BOM
    [Belt Adapter Base (for Anet A8 Toolhead) 1x.stl, Belt Adapter Lid (for Anet A8 Toolhead) 1x.stl, Belt Adapter Lid (for Anet A8 Toolhead) 2x.stl]
2021-06-29 Linear rod clamp of XZ joints now use two screws per rod
    [XZ Axis Left XZ Joint Base 1x.stl, XZ Axis Left XZ Joint Lid 1x.stl, XZ Axis Right XZ Joint Base 1x.stl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]
2021-06-29 The XZ carriage was stiffened; The belt adapter for the Anet A8 toolhead now allows the belt to protrude
    [Belt Adapter Base (for Anet A8 Toolhead) 1x.stl, Belt Adapter Lid (for Anet A8 Toolhead) 2x.stl, XZ Axis Left XZ Joint Base 1x.stl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]
2021-07-04 Minor edits
    [Z Axis Endstop Bracket 1x.stl]
2021-09-04 Redesigned X rod clamps; Added belt tensioning tips to README
    [Belt Adapter Base (for Anet A8 Toolhead) 1x.stl, Belt Adapter Lid (for Anet A8 Toolhead) 2x.stl, XZ Axis Left XZ Joint Base 1x.stl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]
2021-09-05 Reworked Y axis linear rod mounts to reduce number of screws and nuts and printed parts
    [Y Axis Belt Tensioner 1x.stl, Y Axis Belt Tensioner Mount 1x.stl, Y Axis Linear Rod Mount 3x.stl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]
2021-09-05 Added slot nuts to BOM
2021-09-05 Reworked XZ joints
    [XZ Axis Left XZ Joint Back 1x.stl, XZ Axis Left XZ Joint Base 1x.stl, XZ Axis Left XZ Joint Front 1x.stl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]
2021-09-05 Minor XZ joint edits
    [XZ Axis XZ Joint Rod Clamp (45mm) 2x.stl, XZ Axis XZ Joint Rod Clamp (46mm) 2x.stl]
2021-10-31 Minor edits to XZ joint backs
    [XZ Axis Left XZ Joint Back 1x.stl, XZ Axis Right XZ Joint Back 1x.stl]
2021-10-31 Added experimental VORON Afterburner Adapter
    [VORON Afterburner Adapter Left.stl, VORON Afterburner Adapter Right.stl, XZ Axis XZ Joint Rod Clamp (VORON Afterburner) 2x.stl]
2021-10-31 Added images of XZ belt paths
2021-10-31 Naming edits
    [VORON Afterburner Adapter Left 1x.stl, VORON Afterburner Adapter Right 1x.stl]
2021-11-03 Simplified Z axis linear rod mount
    [Z Axis Linear Rod Mount 2x.stl, Z Axis Linear Rod Mount 4x.stl, Z Axis Linear Rod Mount Mirrored 2x.stl]
2021-11-16 Complete redesign of all parts!
    - Simpler and faster to print
    - Less parts, less screws, less nuts
    - Easy-adjustable Z endstop
    - VORON Afterburner compatible via Adapter
    [Belt Adapter Base (for Anet A8 Toolhead) 1x.stl, Belt Adapter Lid (for Anet A8 Toolhead) 2x.stl, VORON Afterburner Adapter Left 1x.stl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]
2021-11-19 Lots of minor design changes; Part renaming; Repository restructuring
    [Belt Tensioner 1x.stl, Belt Tensioner Mount 1x.stl, Left Pulley Mount 1x.stl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]
2021-11-19 Forgot to add files to last commit...
    [Belt Adapter Base (for Anet A8 Toolhead) 1x.stl, Belt Adapter Lid (for Anet A8 Toolhead) 2x.stl, Belt Tensioner 1x.stl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]
2021-11-19 Fixed BOM formatting
2021-11-19 Added XZ belts; New render
2021-11-20 Added belt clamp for VORON Afterburner adapter
    [Belt Adapter Base (for Anet A8 Toolhead) 1x.stl, Belt Adapter Lid (for Anet A8 Toolhead) 2x.stl, Belt Clamp Body 1x.stl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]
2021-11-24 Added firmware tips to README (WIP); Added probe bracket for VORON Afterburner Adapter
    [PL-08N Probe Bracket 1x.stl]
2021-11-24 Flipped pulley lids by 180 degree; Changed 'toolhead' to 'print head'
    [Belt Clamp Body 1x.stl, Belt Clamp Lid 2x.stl, Left Pulley Mount Lid 1x.stl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]
2021-11-27 Slightly adjusted heat insert hole sizes
    [Belt Clamp Body 1x.stl, Left XZ Joint Back 1x.stl, Left XZ Joint Back with Z Endstop Screw 1x.stl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]
2021-11-27 Added missing Y axis parts
    [Belt Tensioner 1x.stl, Belt Tensioner Mount 1x.stl, Nema 17 Mount 1x.stl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]
2021-11-27 Finished BOM
2021-12-03 Replaced all DIN 7991 countersunk by ISO 7380 button head screws; Reinforced upper pulley mounts; Changed color scheme
    [Belt Tensioner 1x.stl, Left Pulley Mount 1x.stl, Left Pulley Mount Lid 1x.stl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]
2021-12-04 All new Y axis motion system!
    [Belt Clamp 1x.stl, Belt Tensioner 1x.stl, Belt Tensioner Mount 1x.stl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]
2021-12-04 Updated belt path images
2021-12-04 Added first accessory
    [Print Head Cable Duct 1x.stl]
2021-12-05 Added LCD controller mount; Added feet
    [Foot 4x.stl, LCD Controller Mount 1x.stl]
2021-12-05 Added warning for Anet A8 board
2021-12-05 Changed project name form 'AM8 plus' to 'AM8 Switchwire Mod' to avoid confusion with Anet A8 plus
2021-12-06 Redesigned Y pulley mount for easier assembly; Added lightweight LM8UU bearing blocks
    [Lightweight LM8UU Bearing Block 7x.stl, Nema 17 Mount 1x.stl, Pulley Mount 1x.stl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]
2021-12-16 Added Switchwire electronics
    [LCD Controller Mount 1x.stl, MeanWell LRS-350-24 Mount 2x.stl.stl]
2021-12-18 Redesigned print head cable duct; Added 2020 cable clip
    [2020 Cable Clip.stl, Print Head Cable Duct 1x.stl]
2021-12-18 Revised 2020 cable clip
    [2020 Cable Clip.stl]
2021-12-25 Some README edits; Added sample klipper config file for SKR Mini E3 V2
    [skr_mini_e3_v2_afterburner.cfg]
2021-12-27 Replaced different Z rod mounts with a single model
    [Left Z Rod Lower Mount 1x.stl, Left Z Rod Upper Mount 1x.stl, Right Z Rod Lower Mount 1x.stl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]
2022-01-30 Changed aluminium extrusions to 2020 B-type nut 6; Redesigned XZ idler pulley mounts; Added f3d and Afterburner CAD files
    [2020 Cable Clip.stl, Belt Clamp 1x.stl, Belt Clamp Body 1x.stl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]
2022-01-30 Updated BOM
2022-01-30 Fixed BOM error
